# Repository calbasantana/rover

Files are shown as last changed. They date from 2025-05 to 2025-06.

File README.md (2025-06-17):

<p align="center">
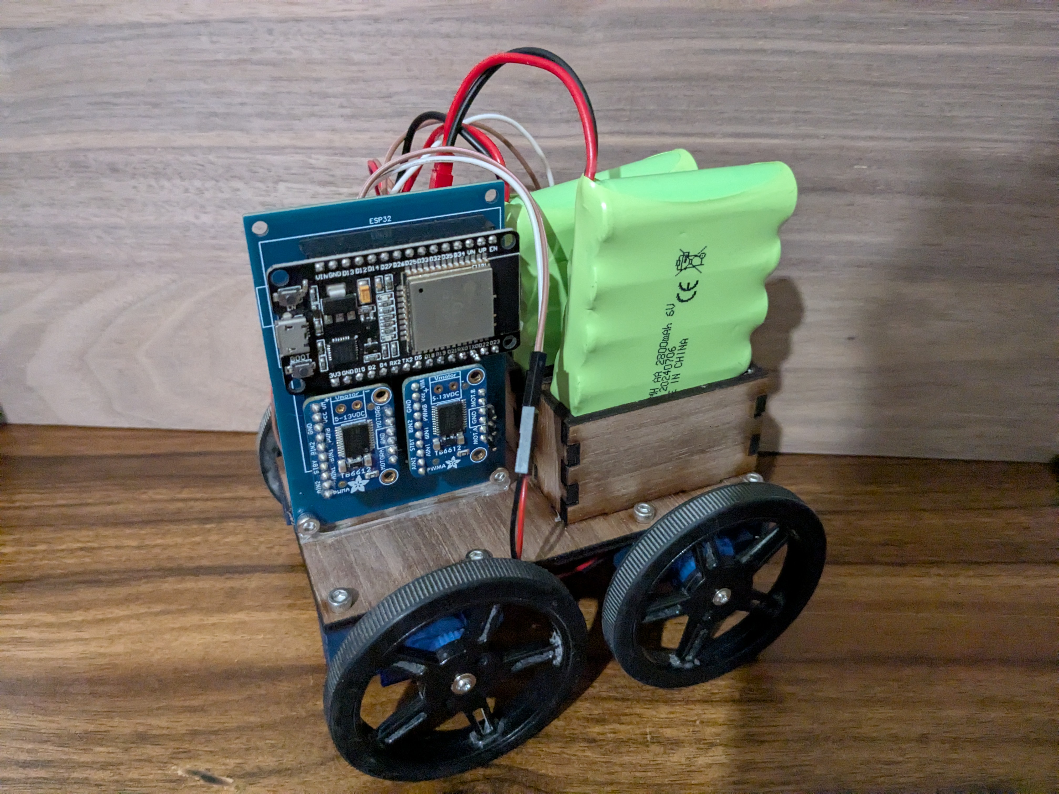
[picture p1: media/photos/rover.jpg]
  
</p>

# Introduction

The purpose of this repository is to provide access to an open-source platform that I have created and developed for students over the last few years as a means of expanding their understanding of physics concepts by applying physics concepts to engineering challenges. This engineering challenge entails the create of a rover - a four- to eight-wheeled vehicle - using an ESP32 microcontroller on a custom PCB.

The engineering challenge has changed over the years, but most recently it has resulted in the development of the companion repository to this repository - the rover challenges arena. Students try to complete up to 10 different challenges with the use of a rover. The present repository covers the construction and coding of the rover.

Below you will find resources associated with this course and repository.

**Associated Resources**:
* [Introductory Physics Google Drive folder](https://drive.google.com/drive/folders/14O6FQSpFUbI4DR4CiFaPI4PMuGjOlXuQ?usp=drive_link)
* [Rover Challenges Arena Repository](https://github.com/calbasantana/rover-challenges-arena)

# Rover Materials

The materials used for this project are broken down into the following components.

## Custom PCB

<p align="center">
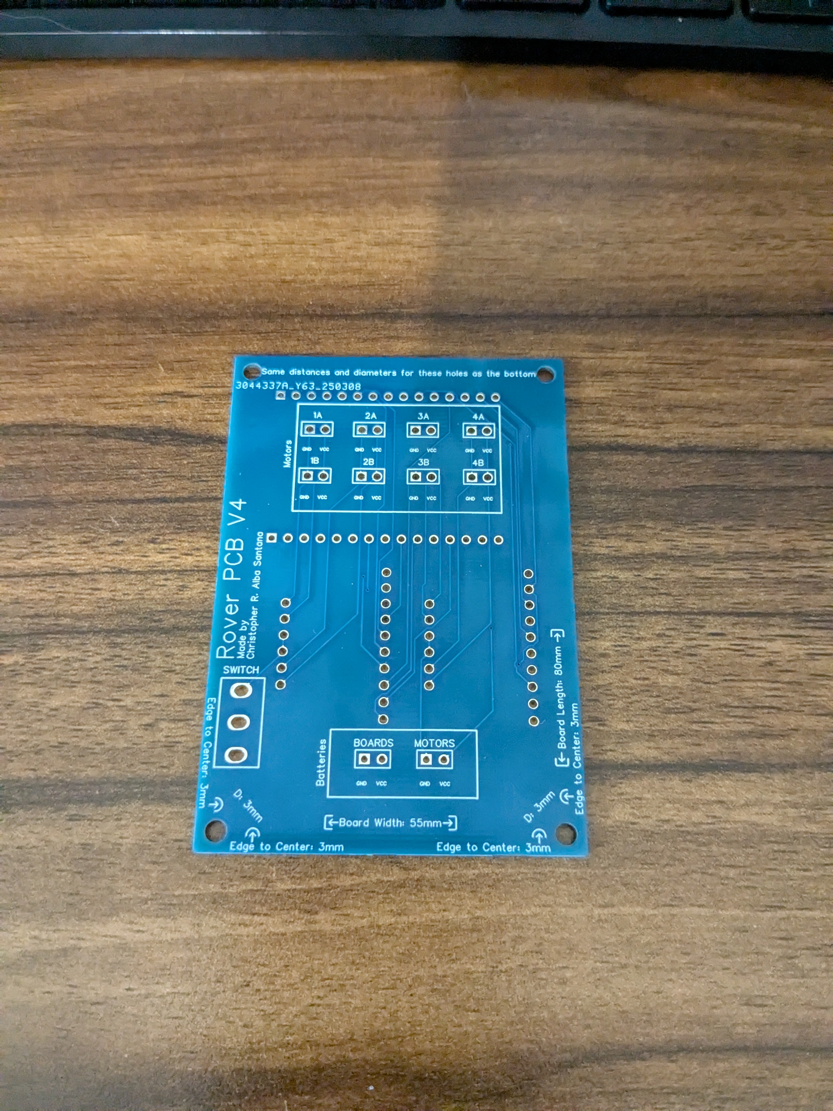
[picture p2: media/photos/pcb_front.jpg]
PCB Front
  
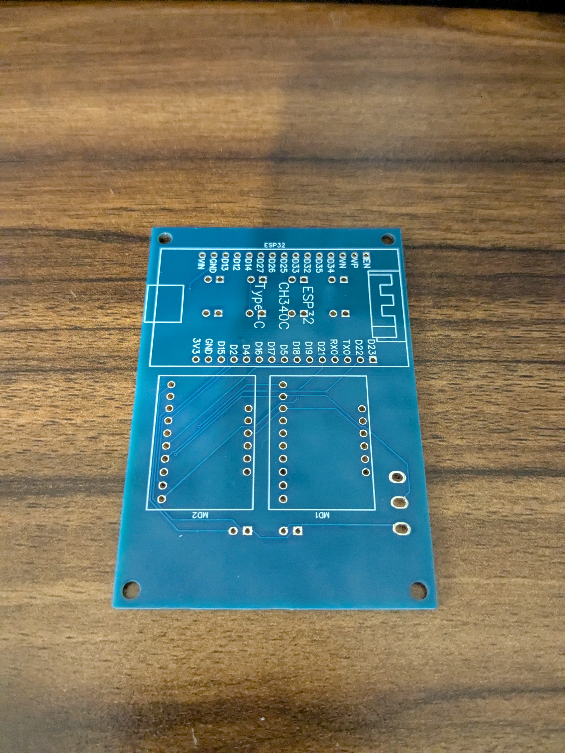
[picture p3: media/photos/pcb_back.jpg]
PCB Back
  
</p>

This custom PCB is designed for an ESP32 to connect to two small motor drivers. It has pins for up to eight motors. However, because each motor driver can only control two motors, this is achieved by making parallel connections to each of the exisiting connections. This means that only four motors can be individually controlled.

This PCB was created using [EasyEDA](https://easyeda.com/). To order a copy of this PCB, uploead the Gerber file from the PCB folder and upload it to [JLCPCB](https://jlcpcb.com/?href=easyeda-home), which is one of many websites that can manufacture PCBs for consumers. They are generally really cheap. As an example, a batch of 50 PCBs costs $19. The only real expensive part is the shipping, usually around $17-50.

The PCB schematic is on the left and the PCB layout is on the right in the images below.

<p align="center">
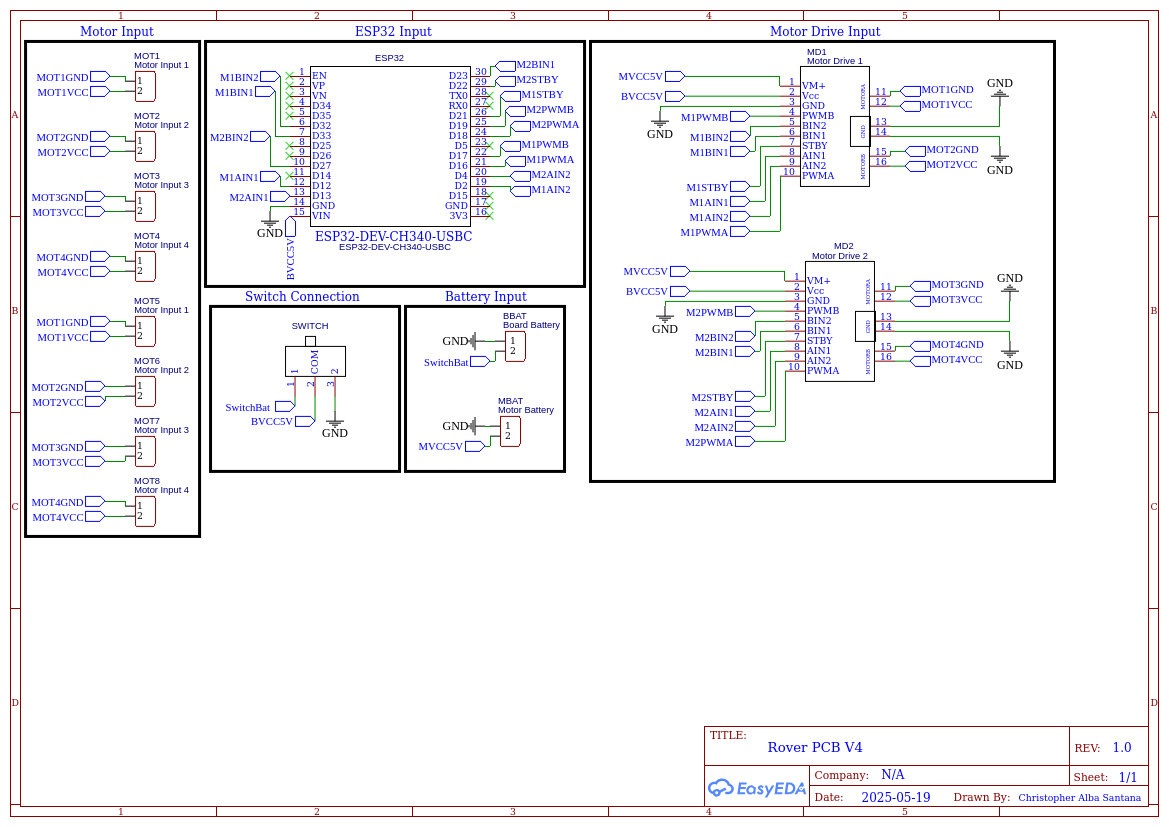
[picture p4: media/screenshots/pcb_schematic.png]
PCB Schematic
  
  PCB Layout
</p>

## Microcontroller, Motors, and Motor Drivers

The following materials need to be purchased for this rover (links included):

* [USB-C ESP32 (X1, $8.99 ea.)](https://www.amazon.com/AITRIP-ESP-WROOM-32-Development-Microcontroller-Integrated/dp/B0DF2YJSHN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)
* [Motor Driver (X2, $6.95 ea.)](https://www.adafruit.com/product/2448)
* [Batteries (X2, $19.99 total)](https://www.amazon.com/dp/B0C5CDZ7HS?ref_=ppx_hzsearch_conn_dt_b_fed_asin_title_3)
* [Battery adapter cables (X2, $1.17 ea.)](https://www.amazon.com/dp/B08SC3D3SQ?ref_=ppx_hzsearch_conn_dt_b_fed_asin_title_1&th=1)
* [DC Motors (X4-X8, $3.50 ea.)](https://www.adafruit.com/product/2941)
* [Wheels (X4-X8, $2.50 ea.)](https://www.adafruit.com/product/2744)
* [Male Header Pins (X16, ~$0.20 total)](https://www.amazon.com/MCIGICM-Header-2-45mm-Arduino-Connector/dp/B07PKKY8BX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)
* [Female Header Pins (X62, ~0.95 total)](https://www.amazon.com/HiLetgo-Single-Female-2-54mm-Vertical/dp/B00VVI1L1W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)
* [Female JST Connectors (X2, ~$0.70 total)](https://www.amazon.com/JST-PH-Connector-Silicone-Cables-Female/dp/B0D7Q9HJLQ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)*
* [Switch (X1, ~$0.40 total)](https://www.amazon.com/dp/B07FVM3XYR?ref_=ppx_hzsearch_conn_dt_b_fed_asin_title_14)
* [M3 x 12mm Socket Screw (X10, ~$0.90 total)](https://www.amazon.com/Socket-Screws-Metric-Stainless-Machine/dp/B07KRRNDGC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)
* [M3 Nut (X2, ~$0.15 total)
](https://www.amazon.com/BinifiMux-100Pcs-0-5mm-Lock-Nuts/dp/B075ZZW7VL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)
* [Male-to-Female cable jumpers (Optional, X4-X8, ~$0.35 ea.)
](https://www.amazon.com/Elegoo-EL-CP-004-Multicolored-Breadboard-arduino/dp/B01EV70C78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)

*: I was not able to find the 2-pin female JST connectors by themselves, so I just used the ones from this bundle.

The above prices are an estimate and does not take into account that if you were to just build one rover, the price would be much higher. However, if you were to assume that you bought enough materials for a class to create somewhere between 5 to 6 rovers, the estimated cost above might make sense on a per rover basis. On average, each rover should cost around **$72.52** (not including the optional cable jumpers, which can allow the rover to be significantly larger). Now, that certainly isn't cheap, but all of these materials can be reused over and over again and if some parts are broken, then they are easy to replace for a few dollars, unlike other platforms that cost upwards of $300 (see [PASCObot](https://www.pasco.com/products/stem-sense/sense-and-control/ps-2994) as an example).

# Rover Body

The rover body needs to be able to hold the most critical parts of the rover, specifically the PCB and batteries. It is also usually the largest single piece of the rover. For this reason, lasercutting is particularly useful. You can not only make large parts without warping, as would occur with 3D printing such a large piece, but you can also make them fast, allowing room for rapid prototyping and fixing of mistakes (because things seldom go right the first time).

## OnShape

To make the body and other parts of the rover, I use [OnShape](https://cad.onshape.com/) and recommend that my students do the same. This is a free online CAD tool, available on all devices and can run even on the most limited of hardware machines.

### OnShape Tutorial

I ask my students to follow an [OnShape Tutorial](https://learn.onshape.com/courses/unit-2-designing-a-skateboard) first, creating a skateboard to familiarize themselves with the tools of OnShape. Most useful are the sketch, extrude, mirror, and dimension tools.

After students have become familiar with OnShape, it is then recommended that they create their own OnShape document and share it out with their group members. While one person will be primarily taking the responsibility of the document, they should all be involved with determining measurements and making design decisions. There will also be days where the lead the designer may be out, so others need to step in their place to continue progress.

### OnShape CAD Model

Below you will see an example of what a rover could look like. This is a very basic design and students can - and should - deviate from it to suit their needs.

<p align="center">
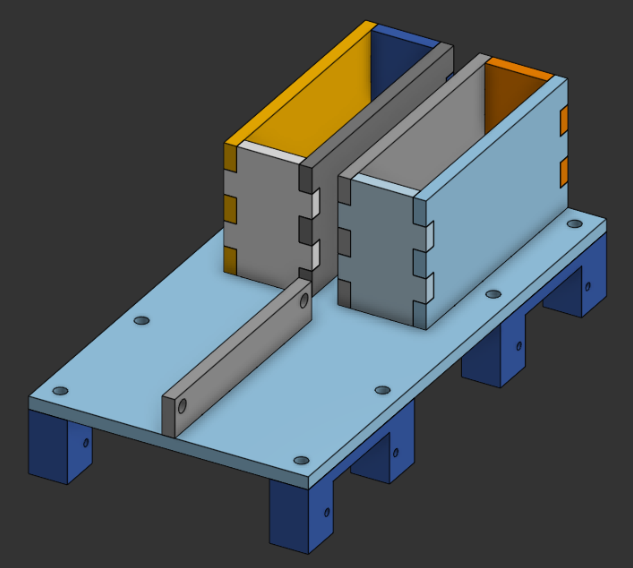
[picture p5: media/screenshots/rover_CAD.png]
Rover CAD Model
  
</p>

Most notable about this design are the following features:

* **Vertical Battery Placement**: The batteries are placed vertically so the rover remains compact.
* **Vertical PCB**: The PCB is placed vertically such that accessing the USB-C port is easier. Additionally, this makes it so that the overall footprint of the base is smaller.
* **Four Motors**: I decided on four motors for simplicity. Having a few additional motors may have been helpful to increase friction for challenges like Challenge 6: Welcome to Seattle, but I decided against it. Should students wish to attempt this challenge, it may be wise to increase the number of motors/wheels.

### Videos for Support

Below you will find videos pertaining to each section of the base design and how they were created. It may be helpful to view them, but students should deviate from this design as needed. Please note these videos are available under media/videos.

**Base and PCB Holder**

https://github.com/user-attachments/assets/f6f469bb-e396-4308-9e46-521faad81ced

**Battery Holders**

https://github.com/user-attachments/assets/219071bb-fc81-4022-aa20-69a2cab3a099

**Motor Mounts**

https://github.com/user-attachments/assets/837b10f8-ceb4-4dcb-96e3-d2f189cb6fed

## Lasercutting and 3D Printing

Most of the rover will be - or at least should be - lasercut. This will make prototyping easier. Out of the previously demonstrated parts, the base, PCB holder, and battery holders components will be lasercut. Motor mounts, due to both their small size and irregular shape, are best 3D printed. Below you will find specifications of the lasercutter and 3D printer used.

### Materials
* [4-Pack 12" x 16" x 1/8" Walnut Plywood Sheets ($23.99)](https://www.amazon.com/ROBOTIME-16-Pack-Walnut-Plywood-Sheets/dp/B0D4QTZWJW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)
* [Navy Blue ELEGOO 1kg, 1.75mm Filament ($18.69)](https://www.amazon.com/ELEGOO-Filament-Dimensional-Accuracy-Carboard/dp/B0CFV4WLY6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)

### Lasercutter
XTool D1 Pro \
**Software** \
XTool Creative Studio (XCS) \
**Settings (for cutting)** \
Power (%): 100 \
Speed (mm/s): 5 \
Pass: 1

### 3D Printer
Original Prusa Mini+ \
**Software** \
PrusaSlicer \
**Settings** \
Layer Height: .2mm \
Infill: 50% \
Supports: Everywhere \
Estimated Printing Time: ~ 2hours.

## Assembly

Once all parts have been lasercut and 3D printed, it is time for assembly. I highly suggest starting off with hot gluing all parts that need to be hot glued and waiting for a bit for them to dry. After doing this, it is recommended to assemble in the following order:

* Place and screw the PCB. Make sure the ESP32 and motor drivers are on it.
* Screw the motor mounts to the board.
* Place the DC motors inside the motor mounts and screw them in, being very careful with their cables. I recommend placing the motors such that the cables coming out of them face towards the center of the rover (this way they won't get caught on stuff).
* Screw the wheels onto the DC motors.
* Connect the motors in the desired locations, using cable jumpers if necessary. **Black goes on GND and red on VCC**. It is recommended to have one motor in each of the numbered slots (like 1A, 2A, 3A, and 4A).
* Connect the battery adapter cables.
* Connect the batteries to test that all components work. **IMPORTANT**: If running the default code, it will have all motors moving forward, so if some wheels are spinning backwards, you can change the orientation of the motor connections such that the black cable is on VCC and red is on GND; **this only works to reverse the drive of motors, do not try this with the batteries**. Remove once you've confirmed all components seem to be working OK. Report any issues.

Here's a video of a rover after assembly and testing.

https://github.com/user-attachments/assets/2081dea4-9fc1-44c9-863f-5ba131637c97

# Programming

Thonny is used as the programming platform. Students can install this application on their own non-chromebook devices using the instructions below.

Go to the official [Thonny](https://thonny.org/) website and download the application. Then, depending on your operating system, continue as follows:

**For Windows**: Install the 64-bit version. Then, go to this [website](https://www.silabs.com/developers/usb-to-uart-bridge-vcp-drivers) to install a driver, which will allow USB access to Thonny so it can connect to the ESP32 via USB. Go to Downloads, then click CP210x VCP Windows. Once downloaded, use the x64 .exe file to install the driver. \
**For Mac**: Install using the first option with .pkg. Then, go to this [website](https://www.silabs.com/developers/usb-to-uart-bridge-vcp-drivers) to install a driver, which will allow USB access to Thonny so it can connect to the ESP32 via USB. Go to Downloads, then click CP210x VCP Mac OSX Driver. Then click on the .dmg file to install; **it will ask you to give access at some point in the settings, make sure to allow it access otherwise it won’t work**. \
**For Linux**: It is recommended that you use the flatpak installation method if you already have flatpak in your system. If you do not have flatpak in your system, you may install it from the terminal via your default package manager; see this [website](https://flatpak.org/setup/) for specific directions if you are unsure. You may need to use “sudo chmod a+rw /dev/ttyUSB0” to open up the USB connection each time you connect the ESP32.

Rovers are programmed in microPython. Below you will find some instructions on how to program the rover, which requires that both .py files in this repostory (main.py and rover.py) are uploaded to the ESP32.

## Programming Your Rover

To program your rover, first open up the Thonny application. Then, follow the instructions below.

1. Remove your ESP32 from your rover. Trying to connect to it while it is connected to the rover might damage the ESP32, so it is best to remove it and then connect to it.

2. Press the STOP/Start button. At the bottom of the screen, you should see ">>>". This should indicate the ESP32 is connected.

3. Go to File -> Open. Select from micropython device. Here, you should be able to open up the main.py file.

4. You should also be able to open rover.py file to see available functions. Essentially, the most important three pieces of code are the following:

  * **rover.move_motor(motor_num, direction, speed)**: You should input the motor number, the direction (forward or backward), and speed (100 - 1000). For example, rover.move_motor(1, forward, 300) moves motor 1 at a speed of 300 forward. You can have multiple motors move at the same time by having them on separate, but sequential lines like so:
    * rover.move_motor(1, forward, 300)
    * rover.move_motor(2, forward, 300) \
  These two lines of code move motors 1 and 2 forward at a speed of 300.
  * **sleep(time)**: This piece of code decides how long the previous piece of code runs for before moving to the next. If placed right after the two pieces of code from the last bullet point, it will move those two motors forward at a speed of 300 for 10 seconds before moving to the next piece of code. Decimals are allowed.
  * **gradual_stop_all(direction="forward", initial_speed=700)**: This piece of code gradually stops all motors. No edits are necessary. However, if you would like to match the speed with the speed from previous line of code, you may do so.

# Frequently Asked Questions

Here are some FAQs from students and my responses.

**ESP32** 

1. **It’s getting warm. What should I do?** A: This ESP32 is no longer usable because it has a shorted circuit somewhere or a component has been damaged. Contact your teacher for a replacement.
2. **There is a blue light that lights up and it won’t move.** A: Unfortunately, this ESP32 is non-functional and you should contact your teacher for a replacement.

**Motors**

1. **The motors won’t move.** A: Check first to make sure that all the motor cables are plugged in. Sometimes they might get loose. If needed, add tape. Additionally, you may want to visually inspect the motors to see if there are any exposed wires on the backside. If the wire is damaged, a replacement motor is necessary, so contact your teacher. If the issue persists, contact your teacher; you may need new motors or the program may be missing from the ESP32.
2. **The motors are moving in the wrong direction. What should I do?** A: While most motors should have their black wires plugged in at GND and their red wires plugged in at VCC, you can change the direction of the motor by switching them. This is only possible with motors, not batteries.
3. **Motor 2 spins slowly compared to the other motors. What should I do?** A: The primary reason for this is that the speed is too high from the programming end. You should change the program to limit maximum speed to 600. Anything above this will result in motor 2 being too slow and cause your rover to drift.

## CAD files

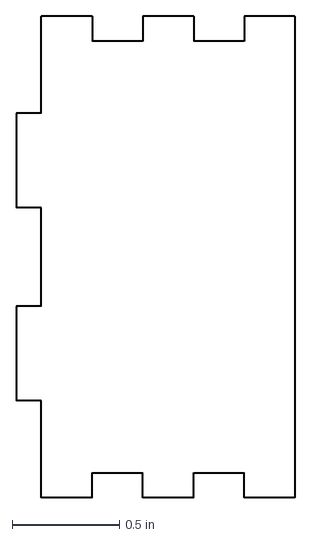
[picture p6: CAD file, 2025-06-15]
CAD Exports/battery_holder_2.dxf
1.30 x 2.24 in

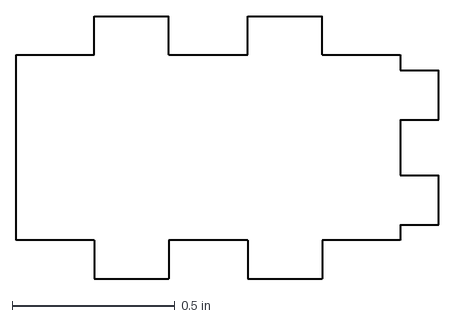
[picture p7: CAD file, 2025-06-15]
CAD Exports/battery_holder_5.dxf
1.30 x 0.807 in

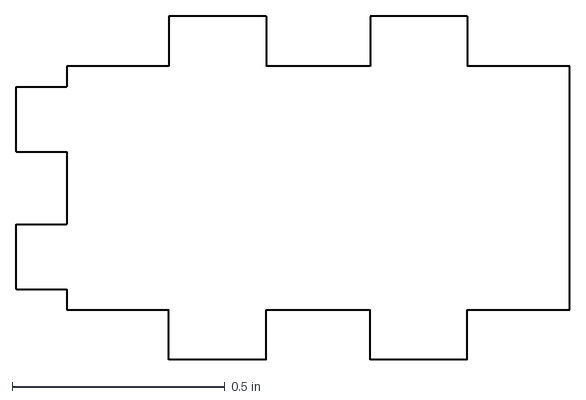
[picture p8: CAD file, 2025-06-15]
CAD Exports/battery_holder_7.dxf
1.30 x 0.807 in

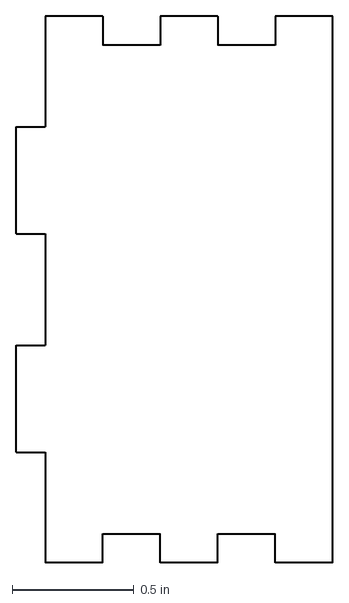
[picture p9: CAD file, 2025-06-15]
CAD Exports/battery_holder_4.dxf
1.30 x 2.24 in

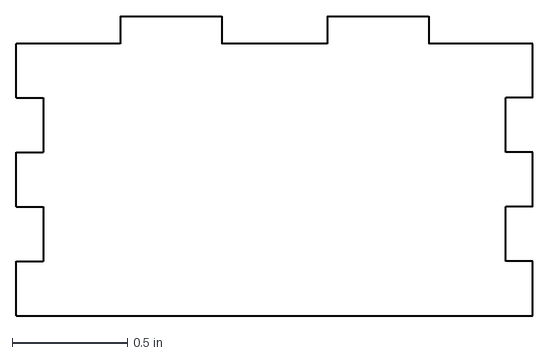
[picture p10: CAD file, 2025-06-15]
CAD Exports/battery_holder_6.dxf
2.24 x 1.30 in

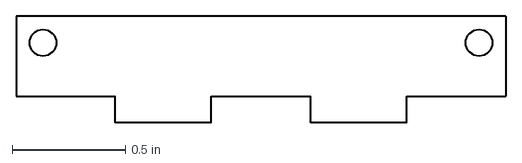
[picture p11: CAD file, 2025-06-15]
CAD Exports/pcb_holder.dxf
2.17 x 0.472 in

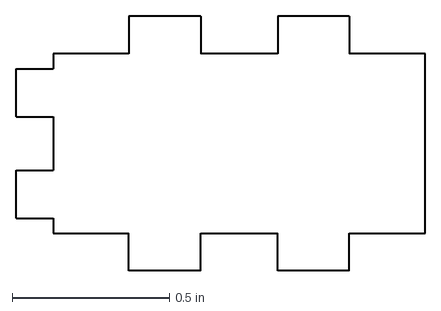
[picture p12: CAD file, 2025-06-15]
CAD Exports/battery_holder_3.dxf
1.30 x 0.807 in

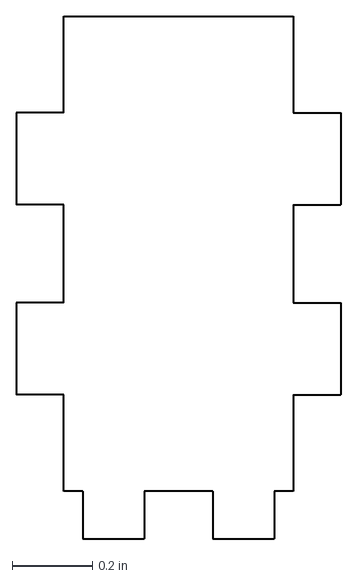
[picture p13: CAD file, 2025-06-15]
CAD Exports/battery_holder_1.dxf
0.807 x 1.30 in

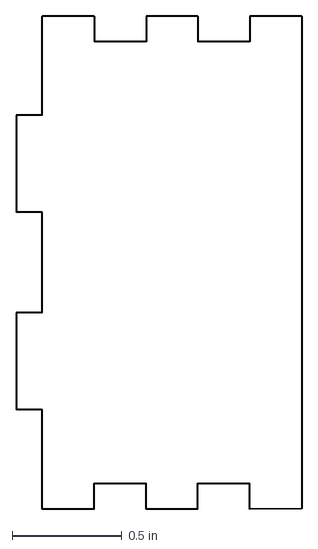
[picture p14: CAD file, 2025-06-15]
CAD Exports/battery_holder_8.dxf
1.30 x 2.24 in

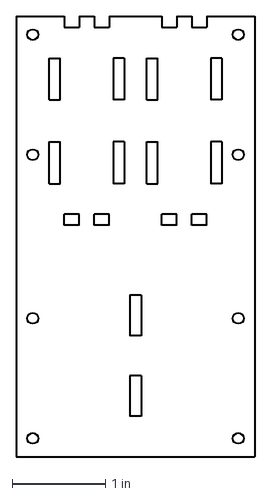
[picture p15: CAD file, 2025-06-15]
CAD Exports/base.dxf
2.56 x 4.72 in

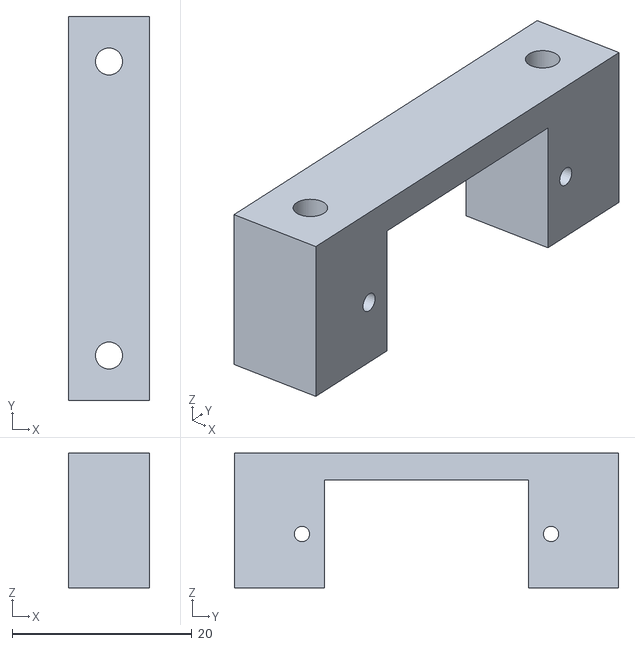
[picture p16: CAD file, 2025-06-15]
CAD Exports/motor_mount.stl
9.00 x 42.7 x 15.0

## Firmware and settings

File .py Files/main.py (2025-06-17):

from rover import MD1, MD2, Rover
from time import sleep

# Setup motor drivers
md1 = MD1(32, 33, 12, 2, 21, 16, 17)
md2 = MD2(27, 23, 13, 4, 22, 18, 19)
rover = Rover(md1, md2)

# Move all motors forward at same speed
rover.move_motor(1, "forward", 600)
rover.move_motor(2, "forward", 600)
rover.move_motor(3, "forward", 600)
rover.move_motor(4, "forward", 600)

sleep(10)

# Stop all motors gradually
rover.gradual_stop_all(direction="forward", initial_speed=700)

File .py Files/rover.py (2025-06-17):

from machine import Pin, PWM
from time import sleep

class MD1:
    def __init__(self, BIN2, BIN1, AIN1, AIN2, STBY, PWMA, PWMB):
        self.bin2 = Pin(BIN2, mode=Pin.OUT)
        self.bin1 = Pin(BIN1, mode=Pin.OUT)
        self.ain1 = Pin(AIN1, mode=Pin.OUT)
        self.ain2 = Pin(AIN2, mode=Pin.OUT)
        self.stby = Pin(STBY, mode=Pin.OUT)
        self.apwm = PWM(Pin(PWMA), freq=50)
        self.bpwm = PWM(Pin(PWMB), freq=50)
        self.stby.value(1)

    def forwardMOT1(self, speed):
        self.bin1.value(1)
        self.bin2.value(0)
        self.bpwm.duty(speed)

    def backwardMOT1(self, speed):
        self.bin1.value(0)
        self.bin2.value(1)
        self.bpwm.duty(speed)

    def stopMOT1(self):
        self.bpwm.duty(0)
        self.bin1.value(0)
        self.bin2.value(0)

    def forwardMOT2(self, speed):
        self.ain1.value(1)
        self.ain2.value(0)
        self.apwm.duty(speed)

    def backwardMOT2(self, speed):
        self.ain1.value(0)
        self.ain2.value(1)
        self.apwm.duty(speed)

    def stopMOT2(self):
        self.apwm.duty(0)
        self.ain1.value(0)
        self.ain2.value(0)

class MD2:
    def __init__(self, BIN2, BIN1, AIN1, AIN2, STBY, PWMA, PWMB):
        self.bin2 = Pin(BIN2, mode=Pin.OUT)
        self.bin1 = Pin(BIN1, mode=Pin.OUT)
        self.ain1 = Pin(AIN1, mode=Pin.OUT)
        self.ain2 = Pin(AIN2, mode=Pin.OUT)
        self.stby = Pin(STBY, mode=Pin.OUT)
        self.apwm = PWM(Pin(PWMA), freq=50)
        self.bpwm = PWM(Pin(PWMB), freq=50)
        self.stby.value(1)

    def forwardMOT3(self, speed):
        self.bin1.value(1)
        self.bin2.value(0)
        self.bpwm.duty(speed)

    def backwardMOT3(self, speed):
        self.bin1.value(0)
        self.bin2.value(1)
        self.bpwm.duty(speed)

    def stopMOT3(self):
        self.bpwm.duty(0)
        self.bin1.value(0)
        self.bin2.value(0)

    def forwardMOT4(self, speed):
        self.ain1.value(1)
        self.ain2.value(0)
        self.apwm.duty(speed)

    def backwardMOT4(self, speed):
        self.ain1.value(0)
        self.ain2.value(1)
        self.apwm.duty(speed)

    def stopMOT4(self):
        self.apwm.duty(0)
        self.ain1.value(0)
        self.ain2.value(0)

class Rover:
    def __init__(self, md1, md2):
        self.md1 = md1
        self.md2 = md2
        self.motors = {
            1: {"driver": md1, "forward": md1.forwardMOT1, "backward": md1.backwardMOT1, "stop": md1.stopMOT1},
            2: {"driver": md1, "forward": md1.forwardMOT2, "backward": md1.backwardMOT2, "stop": md1.stopMOT2},
            3: {"driver": md2, "forward": md2.forwardMOT3, "backward": md2.backwardMOT3, "stop": md2.stopMOT3},
            4: {"driver": md2, "forward": md2.forwardMOT4, "backward": md2.backwardMOT4, "stop": md2.stopMOT4},
        }

    def move_motor(self, motor_num, direction, speed, duration=None, stop_type="brake"):
        if motor_num not in self.motors:
            raise ValueError("Invalid motor number")
        
        motor = self.motors[motor_num]
        if direction == "forward":
            motor["forward"](speed)
        elif direction == "backward":
            motor["backward"](speed)
        else:
            raise ValueError("Invalid direction")

        if duration:
            sleep(duration)
            if stop_type == "brake":
                motor["stop"]()
            elif stop_type == "gradual":
                for s in range(speed, 0, -50):
                    motor["forward"](s if direction == "forward" else -s)
                    sleep(0.05)
                motor["stop"]()
                
    def gradual_stop_all(self, direction="forward", initial_speed=700, step=50, delay=0.05):
        speeds = {motor: initial_speed for motor in self.motors}
        while any(speed > 0 for speed in speeds.values()):
            for motor_num, motor in self.motors.items():
                speed = speeds[motor_num]
                if speed > 0:
                    if direction == "forward":
                        motor["forward"](speed)
                    elif direction == "backward":
                        motor["backward"](speed)
                    speeds[motor_num] = max(0, speed - step)
            sleep(delay)
        for motor in self.motors.values():
            motor["stop"]()

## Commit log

2025-05-19 Update and rename pcb_layout.svg to media/screenshots/pcb_layout.svg
2025-06-15 Update and rename pcb_back.jpg to pcb_back.jpg
2025-06-15 Rename motor_mount.stl to CAD Exports/motor_mount.stl
    [motor_mount.stl]
